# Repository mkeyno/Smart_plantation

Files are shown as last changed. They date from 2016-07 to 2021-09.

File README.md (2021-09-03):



 

# Smart Plantation

My country has limited water resources while most of the farmssteel using the old methods for farming and irrigation. Most of the plantation using 3phase electrical motor for pulling water from deep well, This motor put a heavy load on the electrical grid and the government triedto encourage the farmers to not use the electricity in high peak hours on thegrid by subsidizing those farms which use the electricity in  not rush hours This Repository consists of the hardware and firmware for controllingthe farm water & electricity usage base on IoT technology. The different scenarios can be  set by owners of the plantation regards to the information that comes from the water pumpirrigation systems and lands. 
Water irrigation system consist electrical pump for the well & storagepool, all electrical actuator valve, sensors for soil humidity  and water level in wellSoil humidity detects by a low-power solar humidity sensor equipped with an nRF24lP low power transmitter.Every 3 hours sample of humidity sends to the main unit. Different scenarios base onwater level, time, total electricity consumption will be trigged and report to the landowner via SMS

# Hardware

This controller consists of 4 main modules, 
  - ESP8266 for IoTinterface and local webserver for setting up the plantation control and select a  variety of scenario  
  
  - SIM700 GSM/GPRSmodule for remote control of plantation with a variety of predefined SMS commandwhich is authenticated by mobile number 
  
  - nRF24Lp lowpower transmitter link for gathering data of humidity sensors across theplantation
  
  - STM32F103C8module for handling all sub-control routines such as all valve actuators andmotors and get all sensor information from soil humidity sensor and ultrasonicwater level sensor. 
  
This module activates the electrical motors regards thesensor data and scenario which has been defined by the landowner. To monitor power consumption and power factor of electricalmotors, three ST sensors for measuring the current of each phase, and one transformer formeasuring the voltage of lines has been considered
following are the image of the designed PCB 

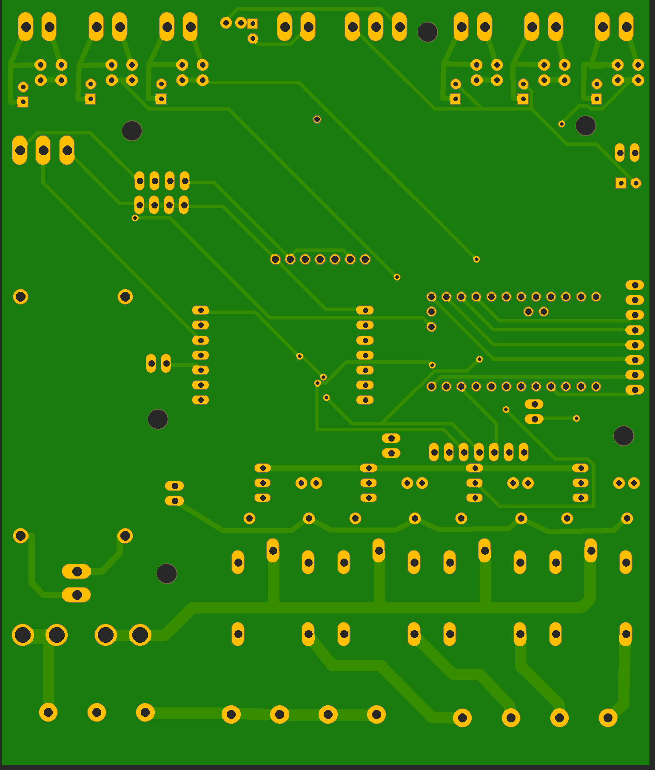
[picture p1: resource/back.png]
,,
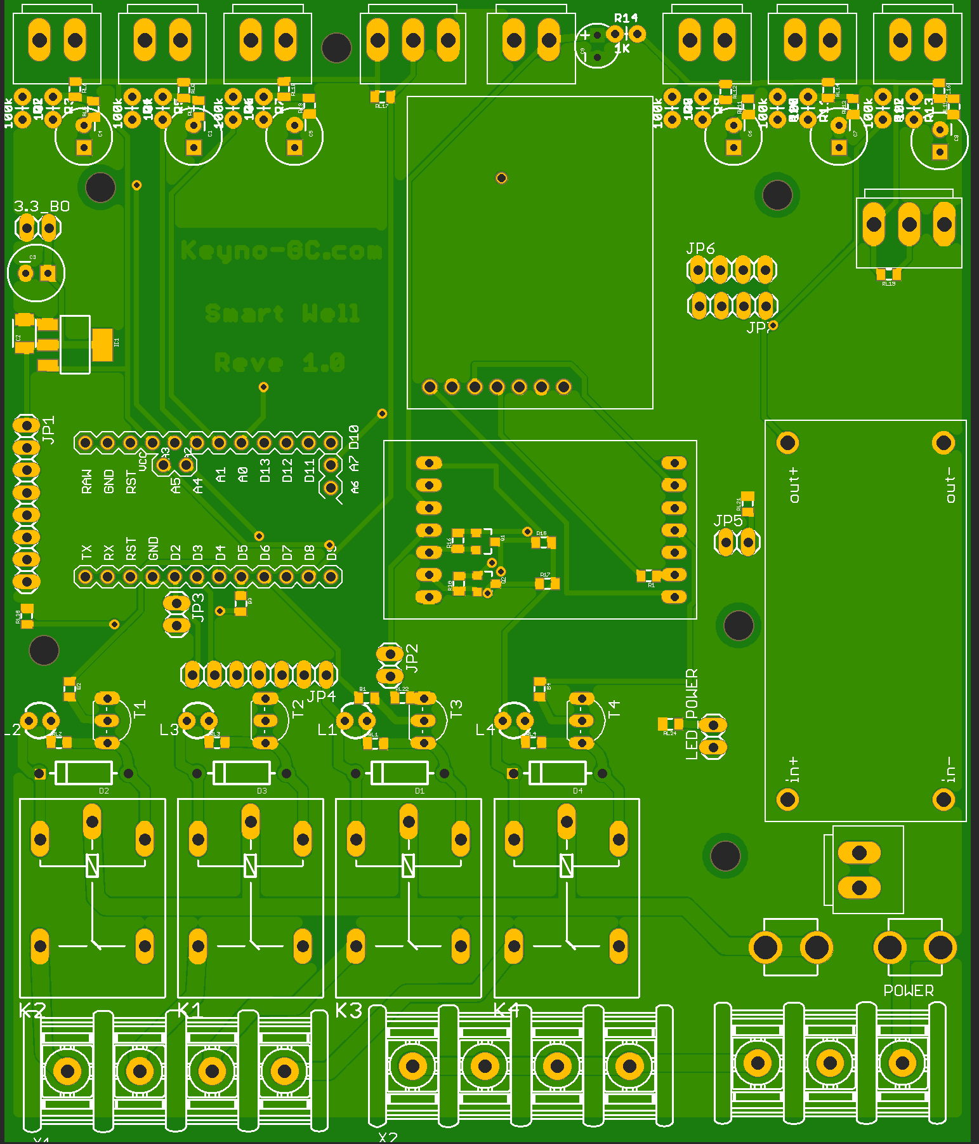
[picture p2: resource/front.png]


# Firmware

Two MCUs were used in this design, one ESP8266 as pilot controland data link  for local webserver and one STM32F103C8 forcontrolling the plantation, these MCUs communicate together via I2C protocol inmaster-slave modeESP8266 can restart the STM32F103C8 and adjust the setting byIOT webserver portal, the following image showing the different pages which designedfor different parts of the controller  

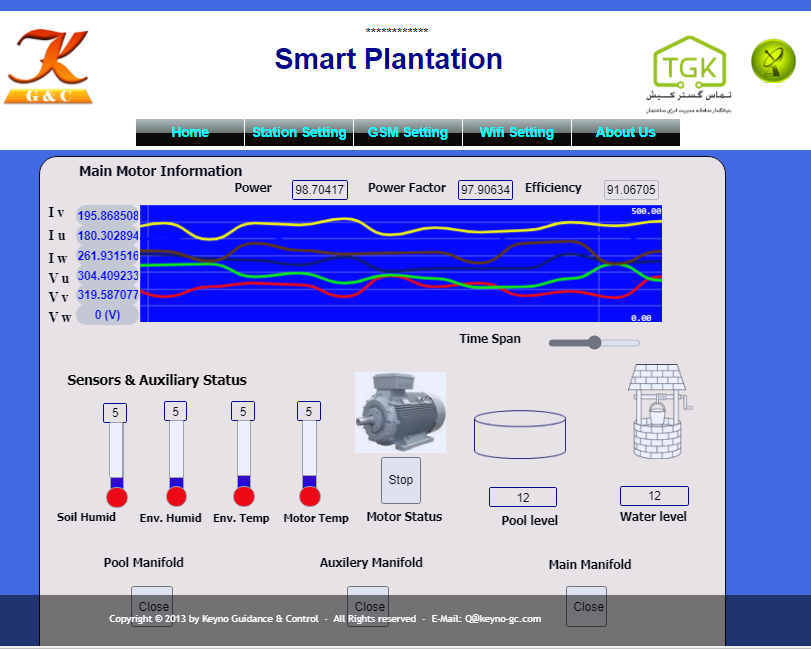
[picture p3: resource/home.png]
 

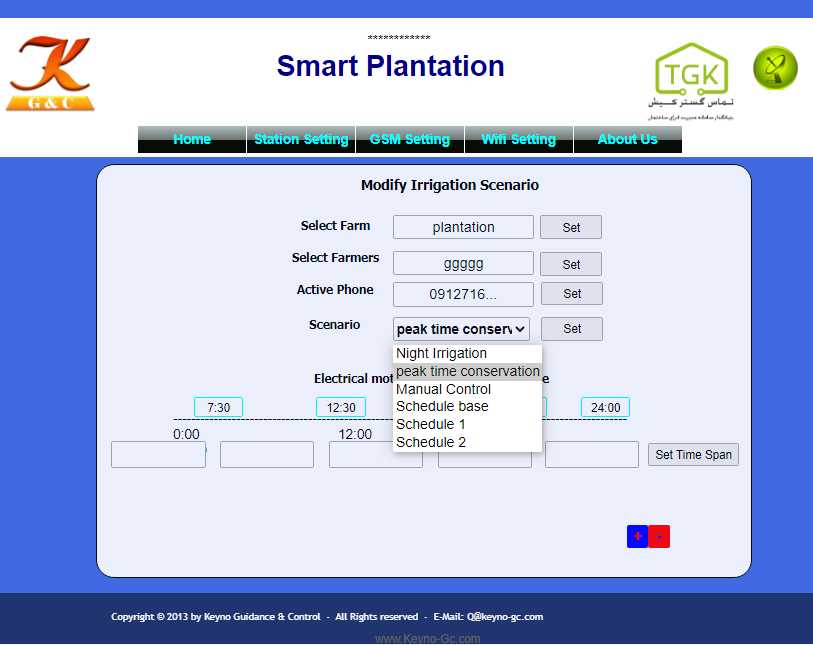
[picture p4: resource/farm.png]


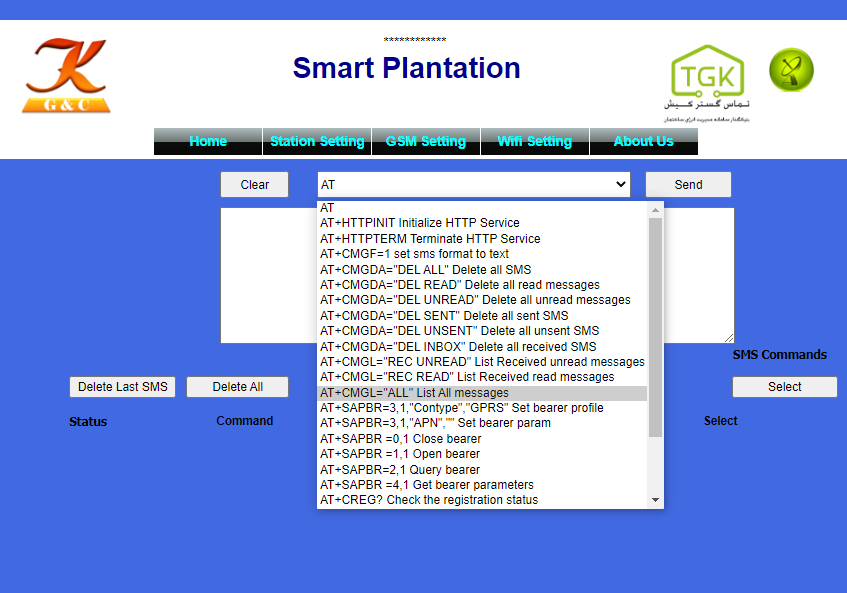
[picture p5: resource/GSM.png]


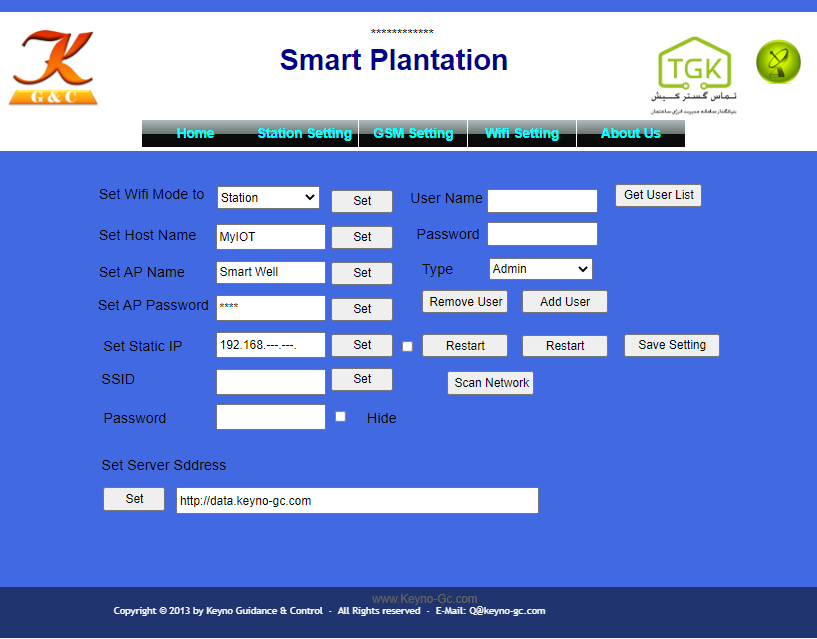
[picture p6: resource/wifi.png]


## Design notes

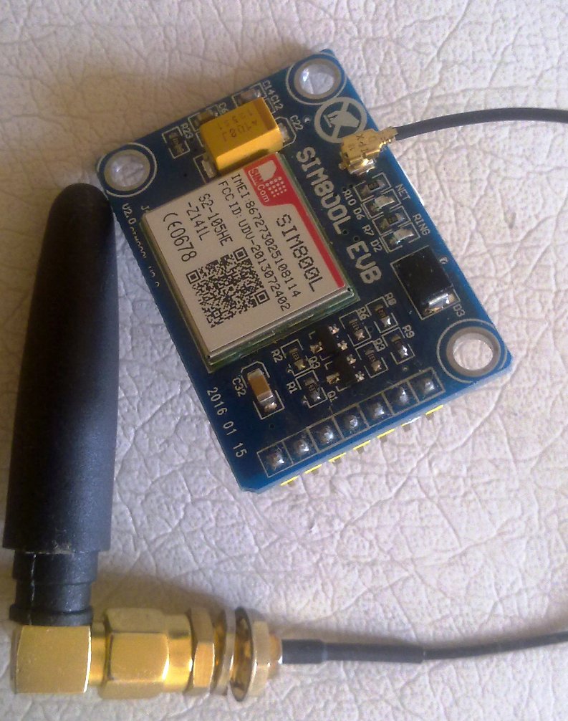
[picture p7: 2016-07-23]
sim.jpg

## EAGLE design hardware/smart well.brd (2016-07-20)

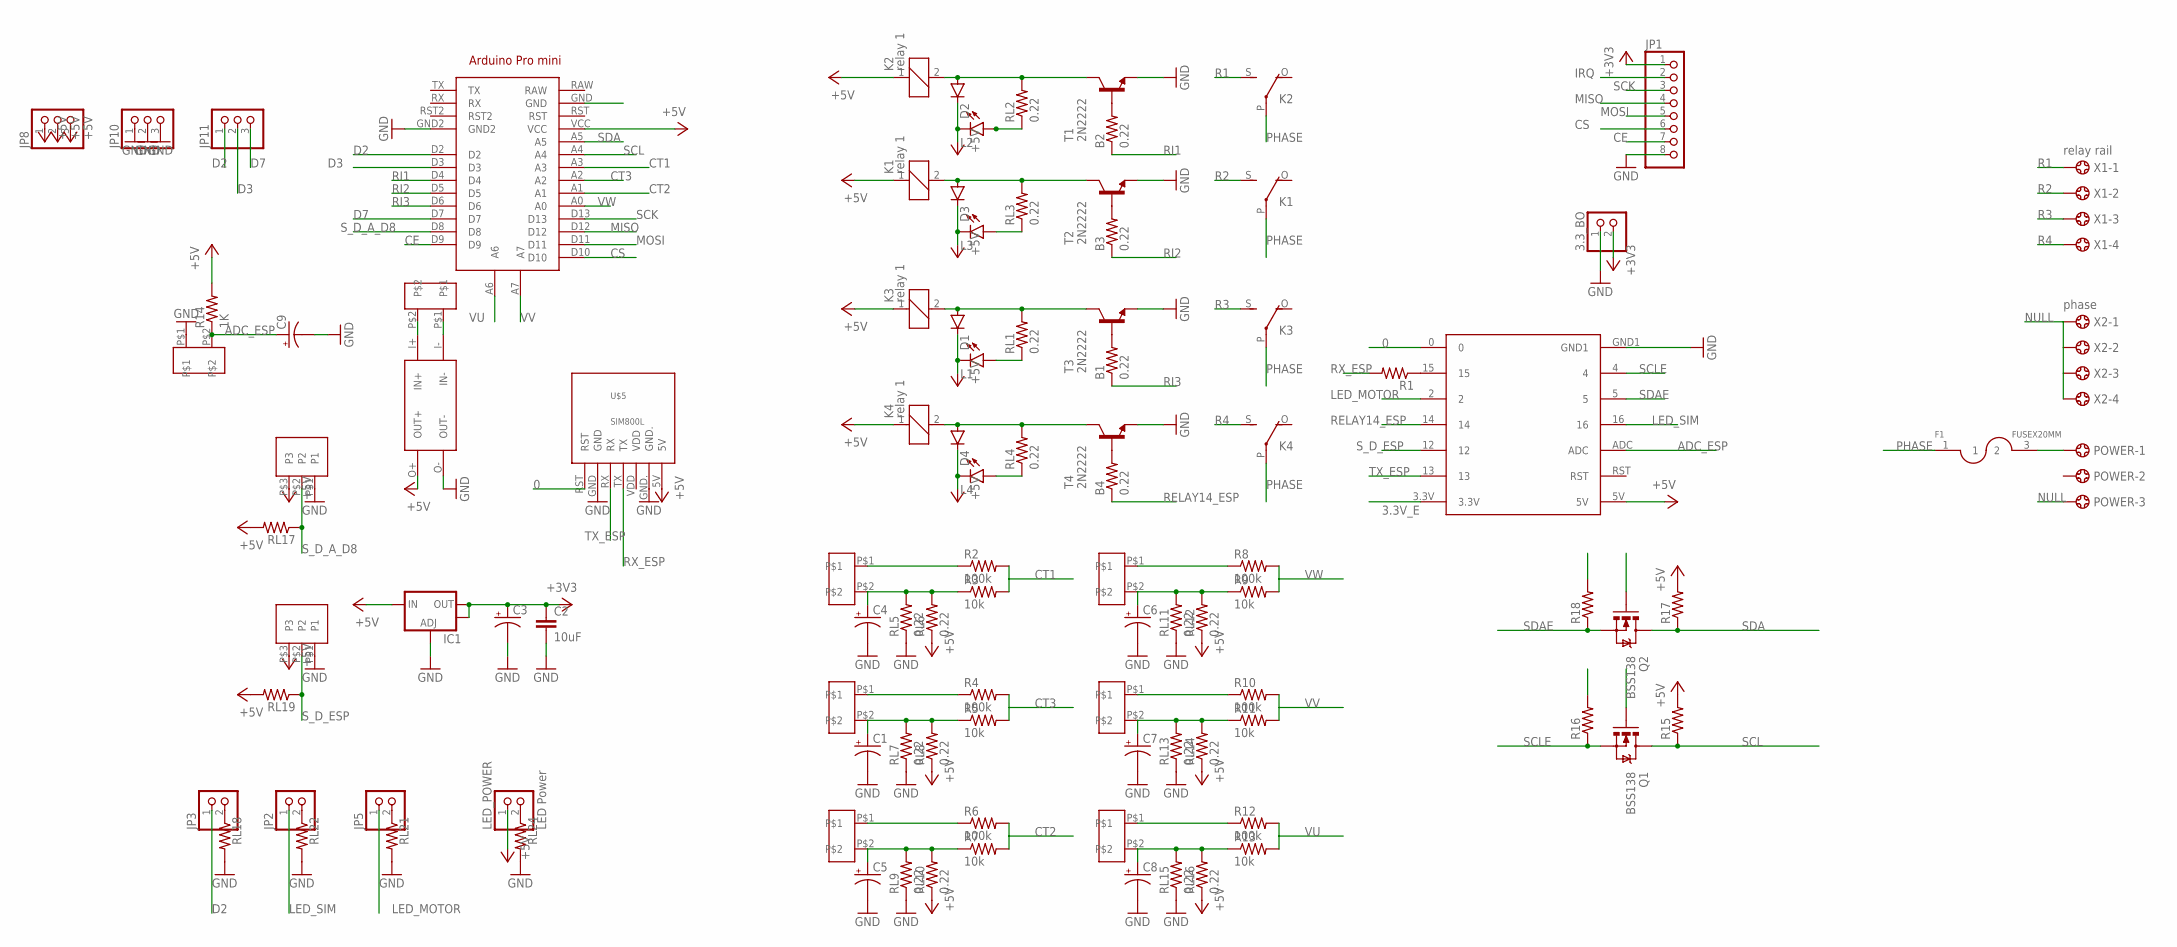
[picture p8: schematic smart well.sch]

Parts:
3.3_BO: PINHD-1X2; 1X02
B1, B2, B3, B4: 0.22; 0805
C1, C3, C4, C5, C6, C7, C8: 100UF-25V-20%(PTH); CPOL-RADIAL-100UF-25V
C2: 10uF; 1210
C9: 10UF-25V-20%(PTH)KIT; CPOL-RADIAL-10UF-25V-KIT
CT1, CT2, CT3, CT4, CT5, CT6: ct1; PIN_LOCK1X2
D1, D2, D3, D4: DIODEKIT2; DIODE-1N4001-KIT
F1: FUSEX20MM; FUSE_5MM
IC1: V_REG_LM1117SOT223; SOT223
JP1: PINHD-1X8; 1X08
JP2, JP3, JP5: PINHD-1X2; 1X02
JP8, JP10, JP11: PINHD-1X3; 1X03
K1, K2, K3, K4: relay 1; G5LE
L1, L2, L3, L4: LED3MM
LED_POWER: LED Power; 1X02
POWER: 5202-03-N-02
Q1, Q2: BSS138; SOT23-3
R1: 0.3OHM-1/8W-1%(0805); 0805
R2, R4, R6, R8, R10, R12: 100k; AXIAL-0.1
R3, R5, R7, R9, R11, R13: 10k; AXIAL-0.1
R14: 1K; AXIAL-0.1
R15, R16, R17, R18: 0.22OHM-1/4W-1%(0805); 0805
RL1, RL2, RL3, RL4, RL5, RL6, RL7, RL8, RL9, RL10, RL11, RL12, RL13, RL14, RL15, RL16: 0.22; 0805
RL17, RL18, RL19, RL21, RL22, RL24: 0.22OHM-1/4W-1%(0805); 0805
T1, T2, T3, T4: 2N2222; TO92-EBC-OVAL
U$2, U$8: PIN_LOCK_1X3; PIN_LOCK1X3
U$3: ESP12F_SHEILD10PIN
U$5: SIM800L
U$6: DC-DC
U$7: ARDUINO_DIP
U$9, U$11: PIN_LOCK_1X2; PIN_LOCK1X2
X1: relay rail; 5202-04-N-02
X2: phase; 5202-04-N-02

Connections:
0: U$3.0, U$5.RST
3.3V_E: Q1.1 (G), Q2.1 (G), R16.2, R18.2, U$3.3.3V
+3V3: 3.3_BO.2, C2.1, C3.1 (+), IC1.2 (OUT), IC1.4 (OUT), JP1.1
+5V: D1.C, D2.C, D3.C, D4.C, IC1.3 (IN), JP8.1, JP8.2, JP8.3, K1.1, K2.1, K3.1, K4.1, L1.K (C), L2.K (C), L3.K (C), L4.K (C), LED_POWER.1, R14.P$2 (2), R15.2, R17.2, RL6.1, RL8.1, RL10.1, RL12.1, RL14.1, RL16.1, RL17.2, RL19.2, U$2.P$3 (P3), U$3.5V, U$5.5V, U$6.O+ (OUT+), U$7.VCC, U$8.P$3 (P3)
ADC_ESP: C9.1 (+), R14.P$1 (1), U$3.ADC, U$11.P$2
CE: JP1.7, U$7.D9
CS: JP1.6, U$7.D10
CT1: R2.P$2 (2), R3.P$2 (2), U$7.A3
CT2: R6.P$2 (2), R7.P$2 (2), U$7.A1
CT3: R4.P$2 (2), R5.P$2 (2), U$7.A2
D2: JP3.1, JP11.1, U$7.D2
D3: JP11.2, U$7.D3
D7: JP11.3, U$7.D7
GND: 3.3_BO.1, C1.2 (-), C2.2, C3.2 (-), C4.2 (-), C5.2 (-), C6.2 (-), C7.2 (-), C8.2 (-), C9.2 (-), IC1.1 (ADJ), JP1.8, JP10.1, JP10.2, JP10.3, RL5.1, RL7.1, RL9.1, RL11.1, RL13.1, RL15.1, RL18.2, RL21.2, RL22.2, RL24.2, T1.E, T2.E, T3.E, T4.E, U$2.P$1 (P1), U$3.GND1, U$5.GND, U$5.GND., U$6.O- (OUT-), U$7.GND2, U$8.P$1 (P1), U$11.P$1
IRQ: JP1.2
LED_MOTOR: JP5.1, U$3.2
LED_SIM: JP2.1, U$3.16
MISO: JP1.4, U$7.D12
MOSI: JP1.5, U$7.D11
unnamed: R1.1, U$3.15
unnamed: U$6.I+ (IN+), U$9.P$2
unnamed: D2.A, K2.2, RL2.2, T1.C
unnamed: D3.A, K1.2, RL3.2, T2.C
unnamed: B2.2, T1.B
unnamed: B3.2, T2.B
unnamed: L2.A, RL2.1
unnamed: L3.A, RL3.1
unnamed: F1.3 (2), POWER.1
unnamed: D1.A, K3.2, RL1.2, T3.C
unnamed: L1.A, RL1.1
unnamed: B1.2, T3.B
unnamed: D4.A, K4.2, RL4.2, T4.C
unnamed: L4.A, RL4.1
unnamed: B4.2, T4.B
unnamed: U$6.I- (IN-), U$9.P$1
unnamed: CT2.P$1, R4.P$1 (1)
unnamed: CT1.P$1, R2.P$1 (1)
unnamed: C4.1 (+), CT1.P$2, R3.P$1 (1), RL5.2, RL6.2
unnamed: C1.1 (+), CT2.P$2, R5.P$1 (1), RL7.2, RL8.2
unnamed: CT3.P$1, R6.P$1 (1)
unnamed: C5.1 (+), CT3.P$2, R7.P$1 (1), RL9.2, RL10.2
unnamed: CT4.P$1, R8.P$1 (1)
unnamed: C6.1 (+), CT4.P$2, R9.P$1 (1), RL11.2, RL12.2
unnamed: CT5.P$1, R10.P$1 (1)
unnamed: C7.1 (+), CT5.P$2, R11.P$1 (1), RL13.2, RL14.2
unnamed: CT6.P$1, R12.P$1 (1)
unnamed: C8.1 (+), CT6.P$2, R13.P$1 (1), RL15.2, RL16.2
unnamed: JP5.2, RL21.1
unnamed: JP2.2, RL22.1
unnamed: LED_POWER.2, RL24.1
unnamed: JP3.2, RL18.1
NULL: POWER.3, X2.1, X2.2, X2.3, X2.4
PHASE: F1.1, K1.P, K2.P, K3.P, K4.P
R1: K2.S, X1.1
R2: K1.S, X1.2
R3: K3.S, X1.3
R4: K4.S, X1.4
RELAY14_ESP: B4.1, U$3.14
RI1: B2.1, U$7.D4
RI2: B3.1, U$7.D5
RI3: B1.1, U$7.D6
RX_ESP: R1.2, U$5.TX
SCK: JP1.3, U$7.D13
SCL: Q1.3 (D), R15.1, U$7.A4
SCLE: Q1.2 (S), R16.1, U$3.4
SDA: Q2.3 (D), R17.1, U$7.A5
SDAE: Q2.2 (S), R18.1, U$3.5
S_D_A_D8: RL17.1, U$2.P$2 (P2), U$7.D8
S_D_ESP: RL19.1, U$3.12, U$8.P$2 (P2)
TX_ESP: U$3.13, U$5.RX
VU: R12.P$2 (2), R13.P$2 (2), U$7.A6
VV: R10.P$2 (2), R11.P$2 (2), U$7.A7
VW: R8.P$2 (2), R9.P$2 (2), U$7.A0

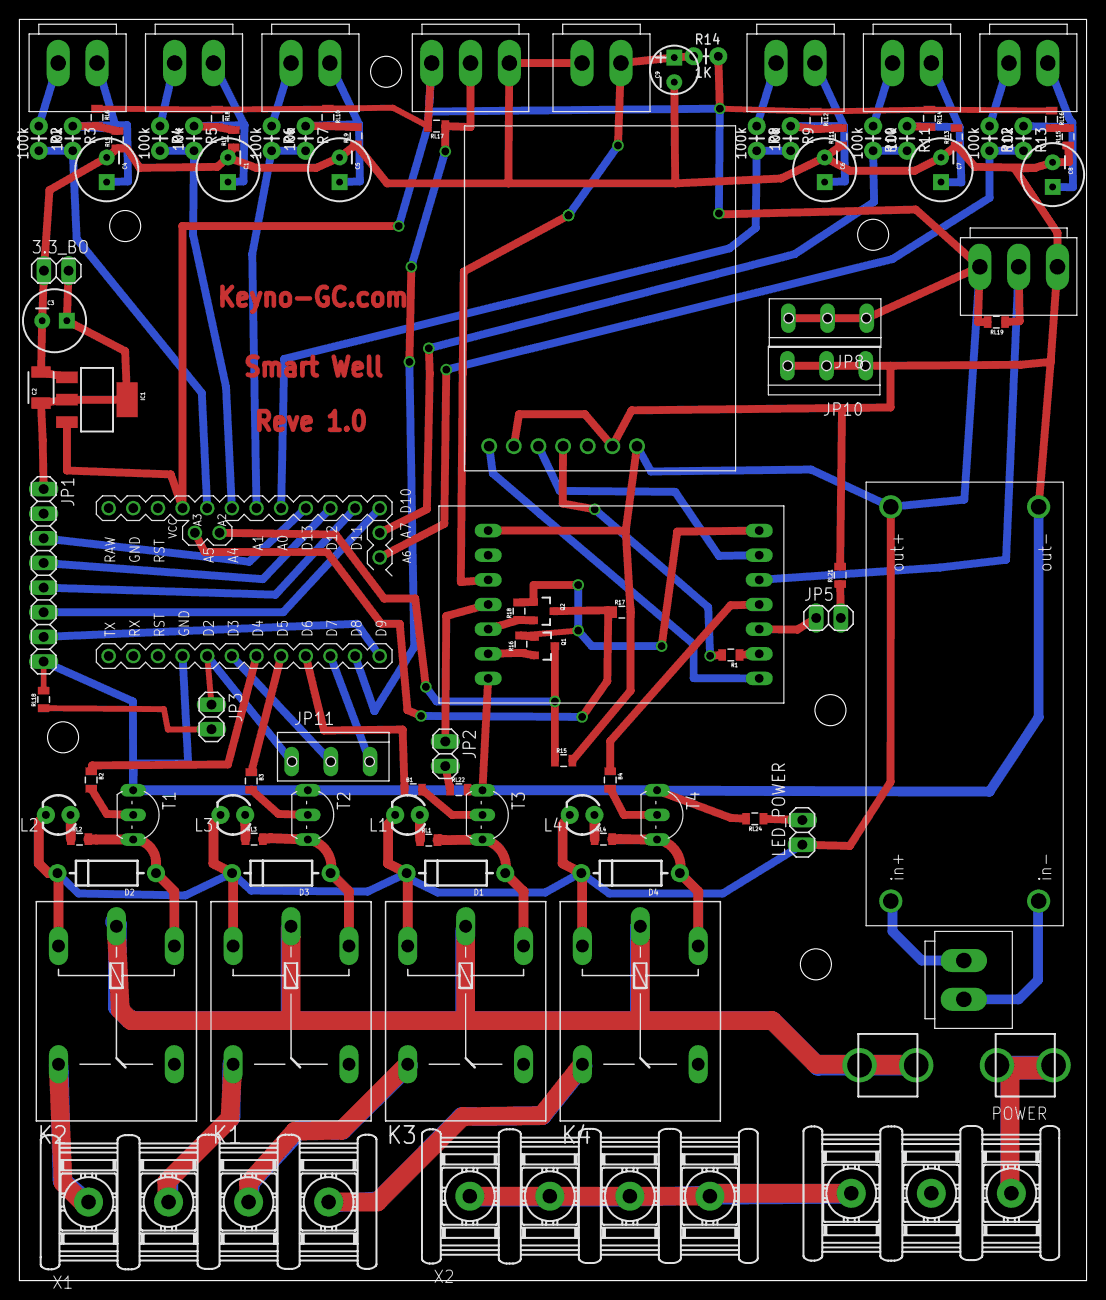
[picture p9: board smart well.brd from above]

Board: 2 copper layers, 110.0 x 130.0 mm, 99 parts (0 on the bottom side), 72 nets.

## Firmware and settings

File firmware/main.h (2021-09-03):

#include <ESP8266WiFi.h>
#include <ESP8266mDNS.h>
#include <ArduinoOTA.h>
#include <time.h>
#include <FS.h>
#include <Hash.h>
#include "ffb.h"
//#include <ESPAsyncTCP.h>
#ifdef EnableUDP
	 #include "ESPAsyncUDP.h"
	 //#include <WiFiUdp.h>
	 #define UDP_PORT       747 
	 #define multicast_PORT 787
	 WiFiUDP _UDP;
	 IPAddress multicast_channel(224,1,1,10);
#endif


#include <ESPAsyncWebServer.h>
		 AsyncWebServer server(80);
		 AsyncWebSocket WS("/ws");
//		  AsyncClient  *client;
//		 AsyncServer Aserver(80);
	//	 AsyncClient  Aclient;		 
//       AsyncEventSource events("/events");
#include <EEPROM.h>
//#define EnableMQTT
 #ifdef EnableMQTT
     #include <AsyncMqttClient.h>
     #include <mqttset.h>
 #endif
 //#define EnableUpdate
#ifdef EnableUpdate
    #include <ESP8266HTTPClient.h>
                     HTTPClient http;				 
    #include <StreamString.h>
    #include <ESP8266httpUpdate.h>
    
     #include <ESP8266HTTPUpdateServer.h>
               ESP8266HTTPUpdateServer httpUpdater;
 #endif
//#include <WiFiClientSecure.h>	
 //         WiFiClientSecure SeClient;	 

 
void setup ( void );
void loop ( void );
#include "htm.h"
#include "param.h"

#include "func.h"
#include "awsocket.h"
#include "async.h"


#include <WiFiClient.h>

 
void setup ( void ) {
 
	 
  Serial.begin(115200);//, SERIAL_8N1,SERIAL_TX_ONLY);
  delay(200);  
  Serial.setTimeout(50);
  //Serial.setDebugOutput(true);
  Serial.print(F("\n\n\n Keyno Guidance & Control\nwww.Keyno-GC.com\nVersion="));  Serial.println(SerialPart); 
  SIM.begin(115200);
  delay(500);
  Wire.begin(SDA_pin,SCL_pin);
 ///////////////////////
 /////////////////////////////////////////////////////////////
 #ifdef DEBUG_Serial1
 Serial1.begin(115200, SERIAL_8N1,SERIAL_TX_ONLY);
 delay(200);
 Serial1.println(F("\n\n\n Keyno Guidance & Control\nwww.Keyno-GC.com\n this is from Serial1"));
 #endif
  
  SPIFFS.begin();
 EEPROM.begin(128);
 delay(100);
   restore_setting();
  // compose_status();
  DIR(); 
  print_chip_info();
  print_device_info();
   wifi_startup();

  if(EnabaleOTA) ConfigureOTA();

   server.on("/exit",             [](AsyncWebServerRequest *request){ ACCESS=ADMIN=false; request->requestAuthentication(); request->send(401, "text/plain", "Thanks\n Exit");  });
server.on("/process", HTTP_GET,[](AsyncWebServerRequest *request){ /*if(Access) */handleProcess(request); });  
server.on("/config",           [](AsyncWebServerRequest *request){ handleConfig(request);  });
server.on("/update", HTTP_GET, [](AsyncWebServerRequest *request){
              if(!check_Auth(request))   request->requestAuthentication(); 
              request->send(200, "text/html", "<form method='POST' action='/update' enctype='multipart/form-data'><input type='file' name='update'><input type='submit' value='Update'></form>");
              });
              
            
server.on("/update", HTTP_POST, [](AsyncWebServerRequest *request){                                                 
                      shouldReboot = !Update.hasError();
                        PRINTF("Update was %s\n",shouldReboot?"OK":"FAIL");
                      AsyncWebServerResponse *response = request->beginResponse(200, "text/plain", shouldReboot?"OK":"FAIL");
                                              response->addHeader("Connection", "close");
                                request->send(response);
  },[](AsyncWebServerRequest *request, String filename, size_t index, uint8_t *data, size_t len, bool final)  {
    if(!index){
        PRINTF("Update Start: %s\n", filename.c_str());
        Update.runAsync(true);
        if(!Update.begin((ESP.getFreeSketchSpace() - 0x1000) & 0xFFFFF000)) Update.printError(Serial);
       }
    if(!Update.hasError()){
              if(Update.write(data, len) != len)      Update.printError(Serial);
            }
    if(final){
        if(Update.end(true))  PRINTF("Update Success: %uB\n", index+len);
        else               Update.printError(Serial);
      }
  }); 
server.on("/upload", HTTP_POST,[](AsyncWebServerRequest *request){ request->send(200, "text/plain", ""); }, handleFileUpload);  
server.onFileUpload([](AsyncWebServerRequest * request, String filename, size_t index, uint8_t *data, size_t len, bool final) {
if (!index)  PRINTF("UploadStart: %s\n", filename.c_str());
PRINTF("%s", (const char*)data);
if (final)  PRINTF("UploadEnd: %s (%u)\n", filename.c_str(), index + len);
});
server.onRequestBody([](AsyncWebServerRequest * request, uint8_t *data, size_t len, size_t index, size_t total) {
if (!index)  PRINTF("BodyStart: %u\n", total);
PRINTF("%s", (const char*)data);
if (index + len == total)  PRINTF("BodyEnd: %u\n", total);
}); 
//server.serveStatic("/", SPIFFS, "/Sindex.html.gz","max-age=86400").setFilter(check_Auth);//.setFilter(FilterStandalone);
/*server.serveStatic("/", SPIFFS, "/Mindex.html.gz","max-age=86400").setFilter(FilterMaster);*/
server.on("/", HTTP_GET, [](AsyncWebServerRequest *request){
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

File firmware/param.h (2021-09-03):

#ifndef _PARAM_H
#define _PARAM_H

extern "C" uint32_t _SPIFFS_start;
extern "C" uint32_t _SPIFFS_end;


 
String Device_info[20];

 
#define   Modes    0
#define   Hostname    1
#define   ST_ssid    2
#define   ST_pass    3
#define   AP_ssid    4
#define   AP_pass    5
#define   Static_IP    6
#define   AP_Server_IP    7
#define   Master_IP    8
#define   Last_store_date    9
#define   Last_store_time    10
#define   MQTT_Server_IP    11
#define   MQTT_Topic    12
#define   MQTT_user    13
#define   MQTT_pass    14
#define   MQTT_port    15
#define   MQTT_clientid    16
#define   Zoon5    17
#define   TempZoon5    18




////////////EEPROM
#define STANDALONE_p      1
#define STATIC_p      2
#define Enable_log_p      3
#define Protcol_p      4
#define _MQTT_p      5
#define QOS_p      6
#define Retain_p      7
#define Send2Server_p      8

#define WheelButtonLeft_p   10
#define WheelButtonRight_p  11
#define GasAxis_p           12
#define BreakAxis_p         13
#define EnableAxisBotton_p  14
#define GasButton_p         15
#define BreakBtton_p        16
#define Calibration_p      30

byte reset_number=0;

byte  STANDALONE=1;
byte  STATIC=0;
byte  Enable_log=0;
byte  COOLINGsys=0;
byte  ReciveRemoteSensor=0;
byte  Protcol=0;
byte  _MQTT=1;
byte  QOS=1;
byte  Retain=1;
byte  Send2Server=0;

 






///////////////////////////////

byte  ZOON=0;
uint32_t TimesSpans[5]={27000,45000,63000,75600,86400};
unsigned long Ego_Seconds=27000;
 
 
String MyIP,MyMAC;
String PerfixID="";
String preSetUser="";
String preSetPass="";
 
byte MainWSclinet;
 

bool shouldReboot = false;   
bool UPDATING=false,PendingUpdating=false;;
bool EnabaleOTA=true; 

 
bool ADMIN=false;
bool ACCESS=false;
String USERS[5],PASS[5],LoginUser;
byte  IsAdmin[5];

 char WifiMode;

 /////////////////////////////////////////////////////////////////////////////////////////////////////////

 /////////////////////////////////////////////////////////////////////////////////////////////////////////
void restor_user_pass(void);
 void UpdateContent(String , String );
  #ifdef EnableMQTT
 void Mqtt_setting(void);
 #endif
 String formatBytes(size_t );
 void print_chip_info(void);
 void print_device_info(void);

 /////////////////////////////////////////////////////////////////////////////////////////////////////////
String read_line(String _path,byte line_num){
File f = SPIFFS.open(_path, "r");
if (!f) return "" ; 
byte counter=0; 
String line="";
while(f.available())//1AAA@THAT54545646|1$15:
{ 
 line = f.readStringUntil('\n'); 
 line.trim();
                         
 if(line.length() >2 && counter==line_num) break;
 counter++;
}
 f.close();  
 return line;
}

String compose(void){
Device_info[Modes]=String(WifiMode);
String s=
Device_info[Modes]+ "@"+
Device_info[Hostname]+ "@"+
Device_info[ST_ssid]+ "@"+
Device_info[ST_pass]+ "@"+
Device_info[AP_ssid]+ "@"+
Device_info[AP_pass]+ "@"+
Device_info[Static_IP]+ "@"+
Device_info[AP_Server_IP]+ "@"+
Device_info[Master_IP]+ "@"+
Device_info[Last_store_date]+ "@"+
Device_info[Last_store_time]+ "@"+
Device_info[MQTT_Server_IP]+ "@"+
Device_info[MQTT_Topic]+ "@"+
Device_info[MQTT_user]+ "@"+
Device_info[MQTT_pass]+ "@"+
Device_info[MQTT_port]+ "@"+
Device_info[MQTT_clientid]+ "@"+
Device_info[Zoon5]+ "@"+
Device_info[TempZoon5]+ "@"+

" ";
PRINTLN(s);
return s;
}



void decompose(String s){
byte As=0; //Modes = WifiMode,Function_Modde,Scenario
 WifiMode=s[0];           if(WifiMode!='S') WifiMode='A'; 
 
   As=s.indexOf('@'); s=s.substring(As+1);
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

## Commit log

2021-09-03 Rename smart well.brd to hardware/smart well.brd
    [smart well.brd]
2021-09-03 Rename smart well.sch to hardware/smart well.sch
    [smart well.sch]

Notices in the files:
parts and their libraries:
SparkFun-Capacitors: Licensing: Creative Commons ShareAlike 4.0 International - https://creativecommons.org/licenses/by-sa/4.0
